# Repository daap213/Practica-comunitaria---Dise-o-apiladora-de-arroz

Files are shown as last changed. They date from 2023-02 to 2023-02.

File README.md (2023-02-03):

# Diseño y análisis de viabilidad de una apiladora de arroz usando energía renovable 

## Ilustració del diseño CAD-Solución:



## Ilustració del circuito:



## Autores ✒

* **Daniel Alvarado Pelaéz** 
* **Marcelo Mendoza Hidalgo**

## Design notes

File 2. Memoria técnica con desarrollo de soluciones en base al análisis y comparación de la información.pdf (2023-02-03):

## Aprovechamiento de recursos para un desarrollo sustentable en Paipayales

## Desarrollo de soluciones en base al análisis y comparación de la

información.

## Integrantes: Marcelo Mendoza Hidalgo, Daniel Alvarado Peláez

Comparación: Potencia, costo y capacidad de piladoras en diferentes mercados.

Se realizó la búsqueda pequeña de diferentes maquinas con la función de pilar arroz,

sea piladoras de múltiples granos, o maquinas moledora, trilladora, piladora de arroz,

## etc. Para así poder comparar principalmente su capacidad de productividad de arroz, el

## requerimiento de potencia del proceso y el costo de la máquina, claro que existen varios

## factores que influyen en el costo y en la potencia requerida, pero esta investigación nos

## dará una idea aproximada de que potencia sería necesaria para cierta capacidad

deseada y el costo que podría tener si se desea adquirir una en el mercado actual.

## Otros factores que se anotaron es la referencia de donde se encontraron las

## maquinarias, cuál era su fuente de energía, a base de combustible como gasolina o

## diésel, o energía eléctrica de 110V, 220V, 380V o 400V y por último el tamaño que cada

proveedor consideraba tenía la máquina.

## Cabe resaltar que la mayoría de estos datos se hallaron en sitios web de comercio

## electrónico como: mercadolibre y Alibaba. Y que no todos contaban todos los campos

## de información que requeríamos, por lo que los gráficos realizados posteriormente se

basan únicamente en aquellas referencias que si cumplen con lo que se desea estudiar.

## Base de datos realizada:

## Tabla 1 Maquinas piladoras: Costo en ($), Potencia en (HP) y capacidad en (Kg/h)

EMPRESA | Tipo | Precio ($) | Potencia (HP) Capacidad (kg/h) DESCRIPCION CODIGO/MODELO/DISTINTIVO TAMAÑO
Torotrac | DIESEL | | 12,00 | 300,00 | MULTIGRANO | PS0000535 | MEDIANA
Torotrac | ELECTRICA 220V | | 2,00 | 150,00 | MULTIGRANO | PS0000989 | PEQUEÑA
Torotrac | GASOLINA | | 5,50 | 150,00 | MULTIGRANO | PS0000983 | PEQUEÑA
Torotrac | DIESEL | | 20,00 | 800,00 | ARROZ GENERICA | PS0000144 | GRANDE
Torotrac | DIESEL | | 20,00 | 800,00 | ARROZ SATAKE | PS0000143 | GRANDE
Torotrac | ELECTRICA 220V | | 2,00 | 220,00 | ARROZ | PS0000145 | PEQUEÑA
Torotrac | GASOLINA | | 5,50 | 160,00 | ARROZ | PS0000991 | PEQUEÑA
Mercado libre | | 2.867,00 $ | 24,00 | 2.000,00 | | JING GU: SB-30GRANDE
Mercado libre | ELECTRICA 220V | 640,00 $ | | 150,00 | ARROZ | | PEQUEÑA
Mercado libre | ELECTRICA 220V | 1.800,00 $ | 15,00 | 1.000,00 | ARROZ | JING GU: SB-10GRANDE
Mercado libre | ELECTRICA 400V | 22.200,00 $ | 14,75 | 5.000,00 | ARROZ | MLGQ36 | GRANDE
Clasf | ELECTRICA 220V | 1.875,00 $ | 3,00 | 300,00 | PILADORA-TRILLADORA DE ARROZ SPHNM-300 | | PEQUEÑA
La Cobacha | ELECTRICA 110V | 650,00 $ | 2,68 | 120,00 | ARROS | POWER BULL: 6N40 PEQUEÑA
Mercado libre | ELECTRICA 220V | 1.195,00 $ | | 300,00 | Trilladora Descascaradora Piladora De Arroz PEQUEÑA
Mercado libre | ELECTRICA 220V | 1.760,00 $ | | 500,00 | ARROZ | | MEDIANA
CROPER | ELECTRICA 220V | | 7,50 | 120,00 | PILADORA-TRILLADORA DE ARROZ PEQUEÑA
Mercado libre | ELECTRICA 220V | 1.800,00 $ | 3,00 | 200,00 | ARROZ | 6N-J40 | MEDIANA
Mercado libre | ELECTRICA 220V | 1.463,00 $ | 3,00 | 150,00 | MULTIGRANO | YUNINLI: J 4 | PEQUEÑA
Mercado libre | ELECTRICA 220V | 1.514,00 $ | 3,00 | 200,00 | MULTIGRANO | YUNINLI: J 40 PEQUEÑA
Mercado libre | ELECTRICA 220V | 1.638,00 $ | 3,00 | 150,00 | MULTIGRANO | YUNINLI: J 220PEQUEÑA
Mercado libre | ELECTRICA 220V | 1.743,00 $ | 4,00 | 200,00 | PILADORA-TRILLADORA DE ARROZ YUNG: J 40 | | PEQUEÑA
Alibaba | ELECTRICA 380V | 2.500,00 $ | 7,40 | 3.000,00 | PILADORA-TRILLADORA DE ARROZ MLGT SERIES Rubber roll husker for rice milling plant GRANDE
Alibaba | ELECTRICA 220V | 2.000,00 $ | 7,40 | 2.000,00 | PILADORA-TRILLADORA DE ARROZ | ANON mini rice huller | GRANDE
Alibaba | ELECTRICA 380V | 4.572,00 $ | 14,75 | 5.600,00 | MULTIGRANO | MLGQ51-001 | GRANDE
Indiamart | | 243,00 $ | 20,00 | 1.000,00 | ARROZ | Dharti | PEQUEÑA
Indiamart | | 243,00 $ | 3,00 | 140,00 | ARROZ | Dharti | PEQUEÑA
Alibaba | ELECTRICA 220V | 120,00 $ | 3,00 | 180,00 | ARROZ | HELI 6N-40 | PEQUEÑA
Alibaba | ELECTRICA 380V | 1.800,00 $ | 30,00 | 2.000,00 | ARROZ | MG-N200 | PEQUEÑA
Alibaba | ELECTRICA 220V | 380,00 $ | 3,00 | 250,00 | ARROZ | HL-6N229 | PEQUEÑA
Alibaba | ELECTRICA 220V | 490,00 $ | 4,00 | 250,00 | ARROZ | KYM-RM6 3/4PEQUEÑA
Alibaba | ELECTRICA 380V | 600,00 $ | 7,40 | 1.500,00 | ARROZ | FORMEND LM24.2C PEQUEÑA
Alibaba | ELECTRICA 220V | 1.000,00 $ | 2,00 | 150,00 | PILADORA-TRILLADORA DE ARROZ DINGXIN 6HW47PEQUEÑA

## Gráficos comparativos:

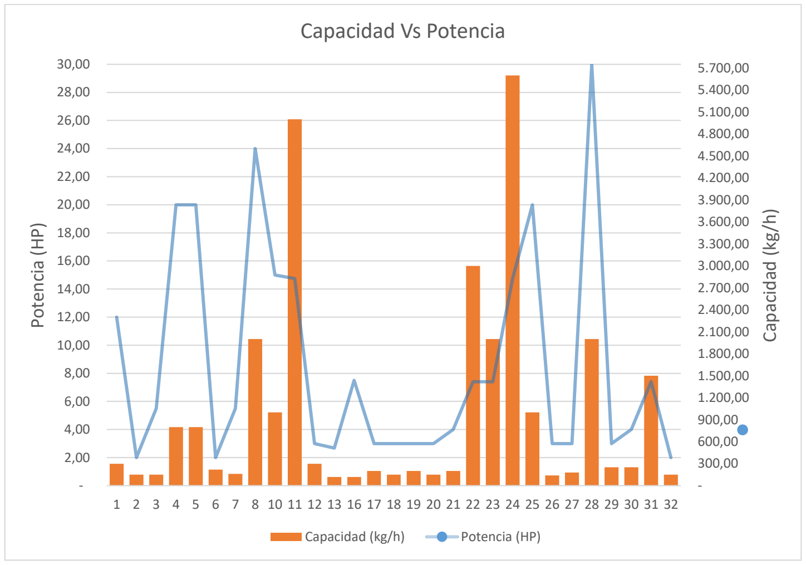
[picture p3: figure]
Capacidad (kg/h); Potencia (HP); Capacidad Vs Potencia

## Este grafico utiliza todos los datos que cuentan con potencia y compara la capacidad de

## la maquina piladora en Kg/h y la potencia que requiere en HP, siendo representados por

columnas y líneas respectivamente.

## La relación potenciada-capacidad es difícil de ver, dado que la potencia que se requiera

## puede aumentar si se realiza funciones además de pilar, como se realiza estos

## procedimientos, y el diseño mismo de la maquina influye en la eficiencia con la que se

## utiliza la potencia. Aun así en las algunas zonas donde las columnas seguidas de

capacidad tienden al mismo, la potencia también tiende a un mismo valor.

1 2 3 4 5 6 7 8 10 11 12 13 16 17 18 19 20 21 22 23 24 25 26 27 28 29 30 31 32

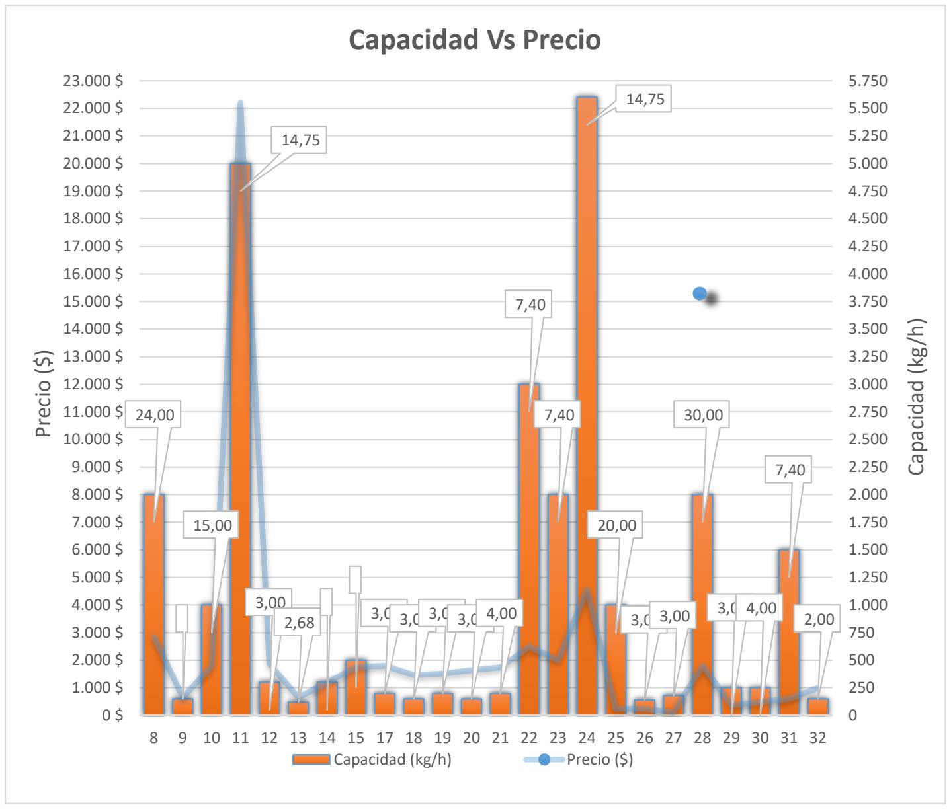
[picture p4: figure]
Capacidad (kg/h); Precio ($); Capacidad Vs Precio

## Este grafico utiliza todos los datos que cuentan con precio y compara la capacidad de la

## maquina piladora en Kg/h y el valor que tiene, siendo representados por columnas y

## líneas respectivamente, además en caso de que la maquina tenga registrada su

potencia, esta aparece como etiqueta.

## En general se aprecia que los puntos más altos de capacidad varían enormemente con

## el precio, debido a que han de contar con otras funciones o mejor calidad en cuanta

## maquinaria, pero con capacidades bajas como de 600 Kg/h se puede observar una

tendencia más estable.

2,68 3,00 3,00 3,00 3,00 4,00 | 3,00 3,00 | 3,00 4,00 | 2,00

8 9 10 11 12 13 14 15 17 18 19 20 21 22 23 24 25 26 27 28 29 30 31 32

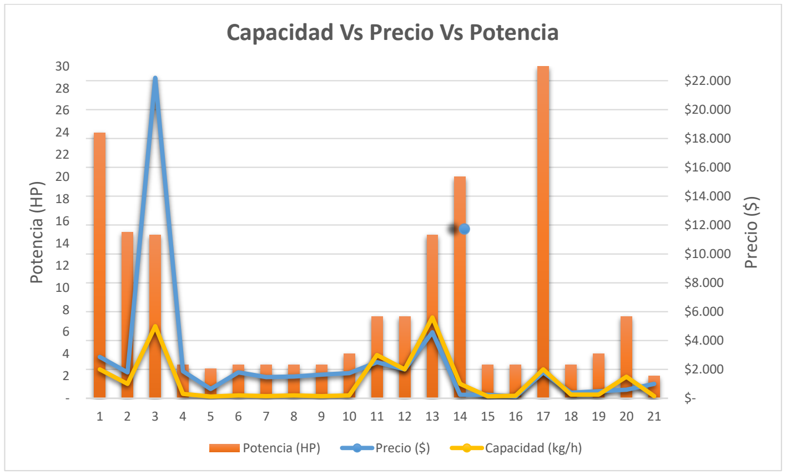
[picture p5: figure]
Potencia (HP); Precio ($); Capacidad Vs Precio Vs Potencia; Capacidad (kg/h)

## En este último grafico se utilizan todos los datos que cuentan con precio y potencia para

## comparar el costo de la maquina versus la potencia que requiere, siendo representados

## por líneas azules y columnas anaranjadas respectivamente, además la capacidad de la

## maquina piladora se ve representada con líneas amarillas, aunque no cuenta con una

## representación numérica, sirve para dar una idea de la relación potencia-costo-

capacidad.

## Se puede observar que para potencias menores a 8 HP, los precios tienen cierta

## tendencia estable, Lo que nos una idea de que valor podría tener una pilladora que

requiera 3HP, además en conjunto la capacidad de 100 kg/hora requerida.

1 | 2 | 3 | 4 | 5 | 6 | 7 | 8 | 9 10 11 12 13 14 15 16 17 18 19 20 21

Referencias:

### https://es.scribd.com/document/380323860/Modelos-de-Maquinas-Piladoras-Arroz

### https://www.sangatiberga.com.br/es/produtos/arrozeras/descascaradora-de-arroz-sbr-sd

### https://www.torotrac.com/product/OE-Piladora%20de%20Maiz-%20Piladora%20de%20Cafe%20-%20Piladora%20de%20Arroz

### https://www.torotrac.com/product/OE-Piladora-2

### https://www.torotrac.com/product/OE-Moledora-PS0000981

### https://www.torotrac.com/product/OE-Piladora-1

### https://www.torotrac.com/product/OE-Piladora-PS0000980

### https://www.torotrac.com/product/OE-Piladora-PS0000989

### https://es.made-in-china.com/co_ueindus/product_Mini-Small-Rice-Mill-for-Home-Use_rgieeurng.html

### https://www.suriaenergy.com/de-motores-electricos-y-energia-solar

### https://www.muyinteresante.es/innovacion/articulo/motores-stirling-para-obtener-energias-renovables

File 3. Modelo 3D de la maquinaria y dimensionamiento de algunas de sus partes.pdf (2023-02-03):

Aprovechamiento de recursos para un desarrollo sustentable en Paipayales

Dimensionamiento y diseño de prototipo de bajo costo.

Integrantes: Marcelo Mendoza Hidalgo, Daniel Alvarado Peláez

Diseño Inicial de Piladora de Arroz

Se realizó el dibujo inicial de la piladora de arroz la cual debe producir 1 quintal de arroz

por hora. En base a los datos presentados previamente y a investigaciones anteriores,

se hizo la comparación de producción de arroz y de motores en base a su potencia,

estableciendo que el motor que se usará para nuestra aplicación será un motor de 3HP

que en próximos avances se revisará su implementación con energías renovables.

Con este dato se investigó diseños de piladoras que posean esa potencia, con ello se

tuvo una idea de la forma y tamaño adecuado aproximado que tendrá nuestro diseño el

cual se presenta a continuación (dimensión del motor sujeta a cambios):

Mesa de trabajo:

En esta pieza se asienta la máquina piladora se realizará del material adecuado para

absorber vibraciones

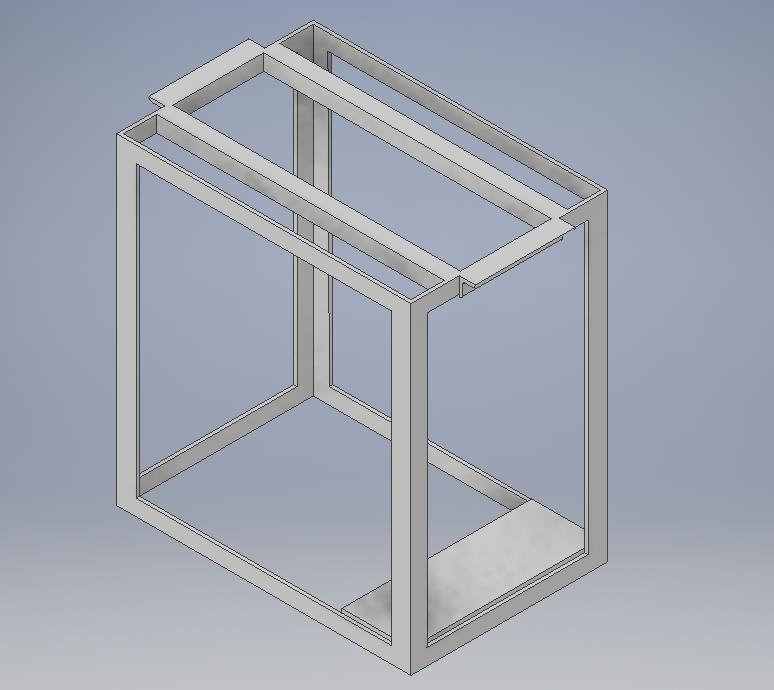
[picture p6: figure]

Parte exterior de la máquina:

Se puede observar en la parte superior el “embudo” en donde se colocará los granos de

arroz a descascarar, esta pieza sirve de carcasa para la parte interna de la máquina en

donde se separa el arroz de su cáscara.

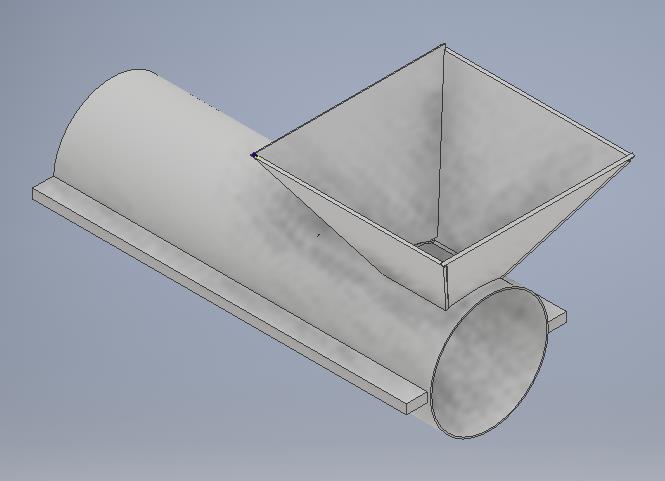
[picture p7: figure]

Eje de moler:

Esta parte de la máquina en su parte giratoria en forma de espiral se encarga de empujar

el arroz que ingresa y a continuación molerlo o desprenderlo de su cáscara mediante las

partes más salidas del eje que tienen contacto con la carcasa mientras sigue con el

recorrido

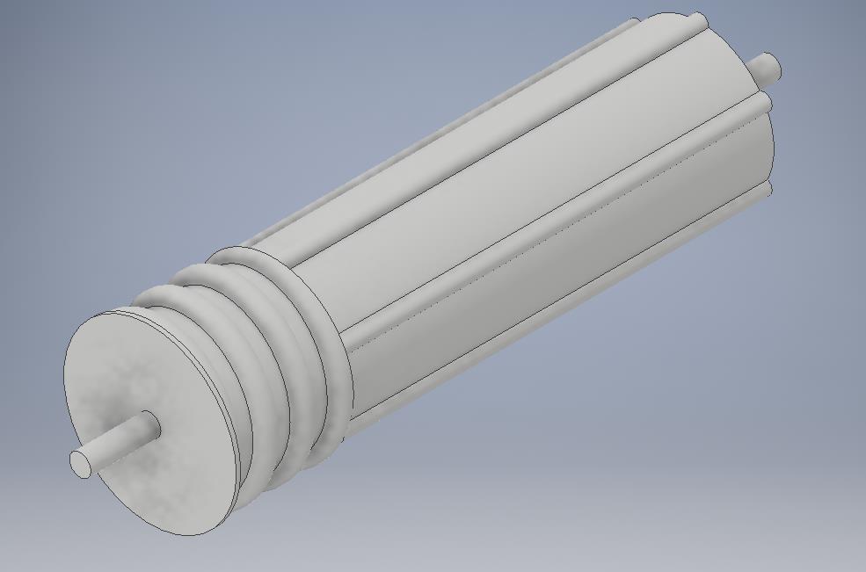
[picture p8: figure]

Pieza Cernidera:

Esta pieza se encuentra alrededor del eje de moler, la cual permitirá el paso de la

cáscara del arroz y no del arroz descascarado (como una cernidera). Con ello se puede

expulsar la cáscara del arroz por la parte de abajo de la máquina y permitiendo el paso

del arroz hacia el final del avance del eje en donde se encuentra una salida para el

arroz sin cáscara.

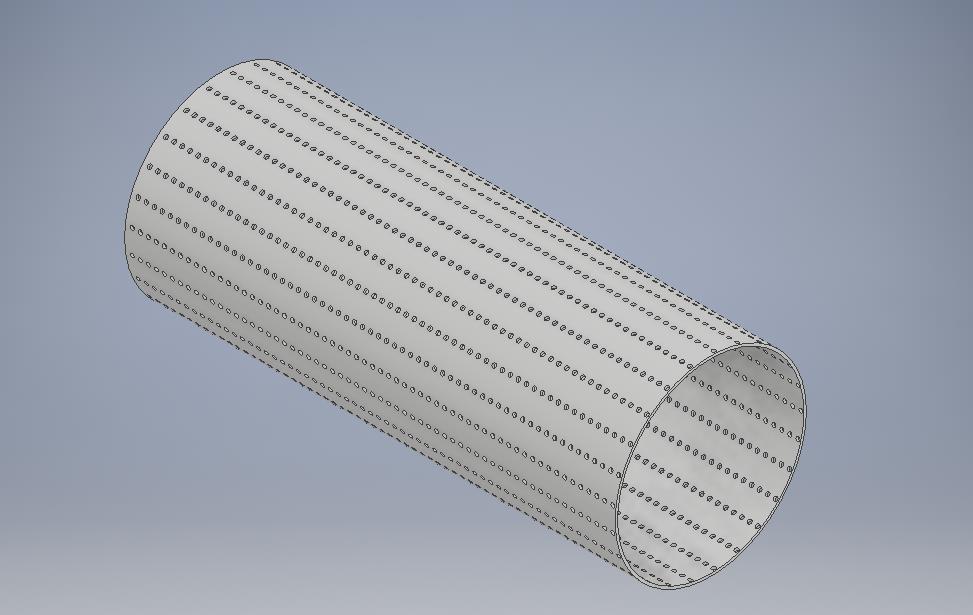
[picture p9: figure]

Ensamblaje:

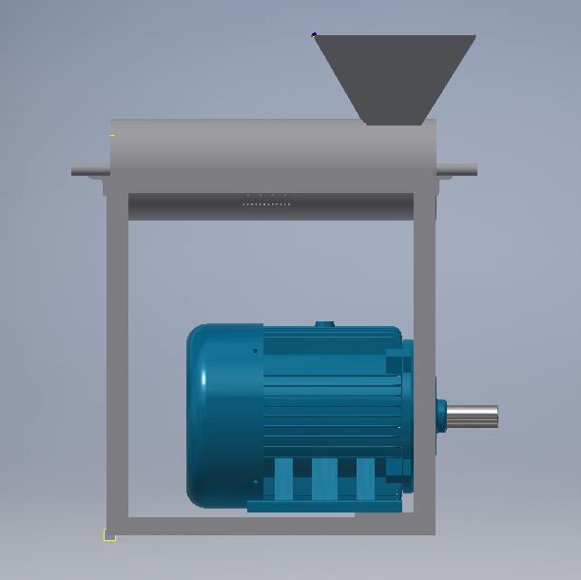
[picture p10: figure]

Aplicándole transparencia a la carcasa:

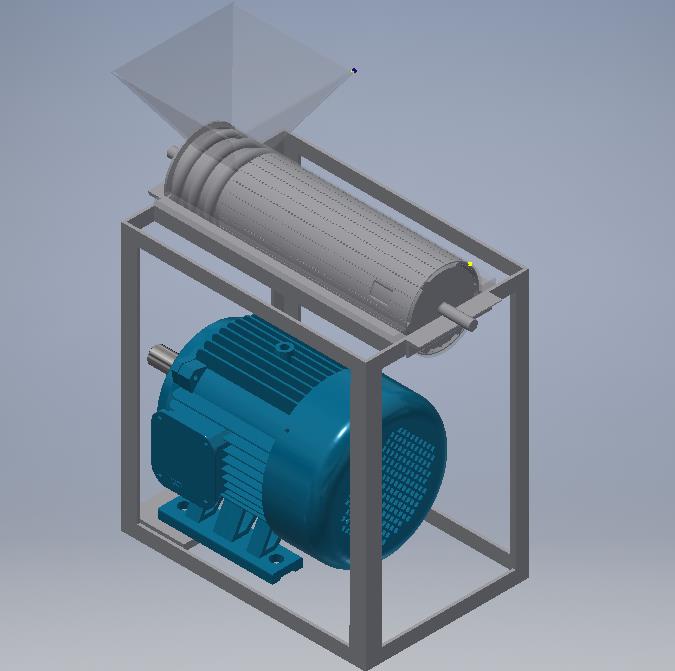
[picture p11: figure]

Aplicándole transparencia a la carcasa y cernidera:

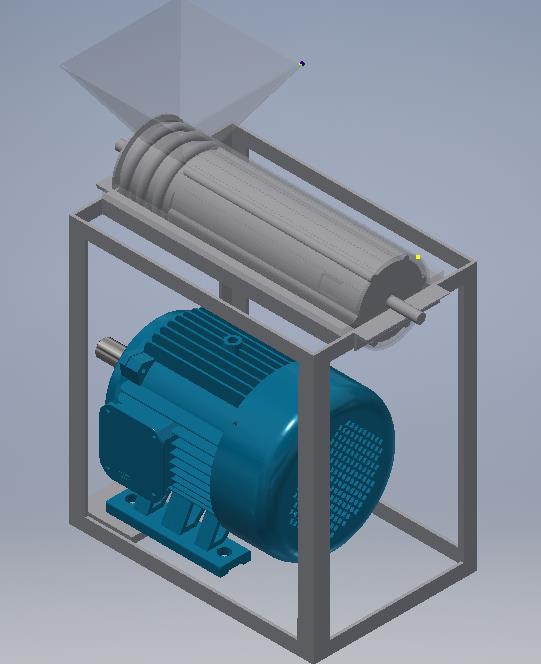
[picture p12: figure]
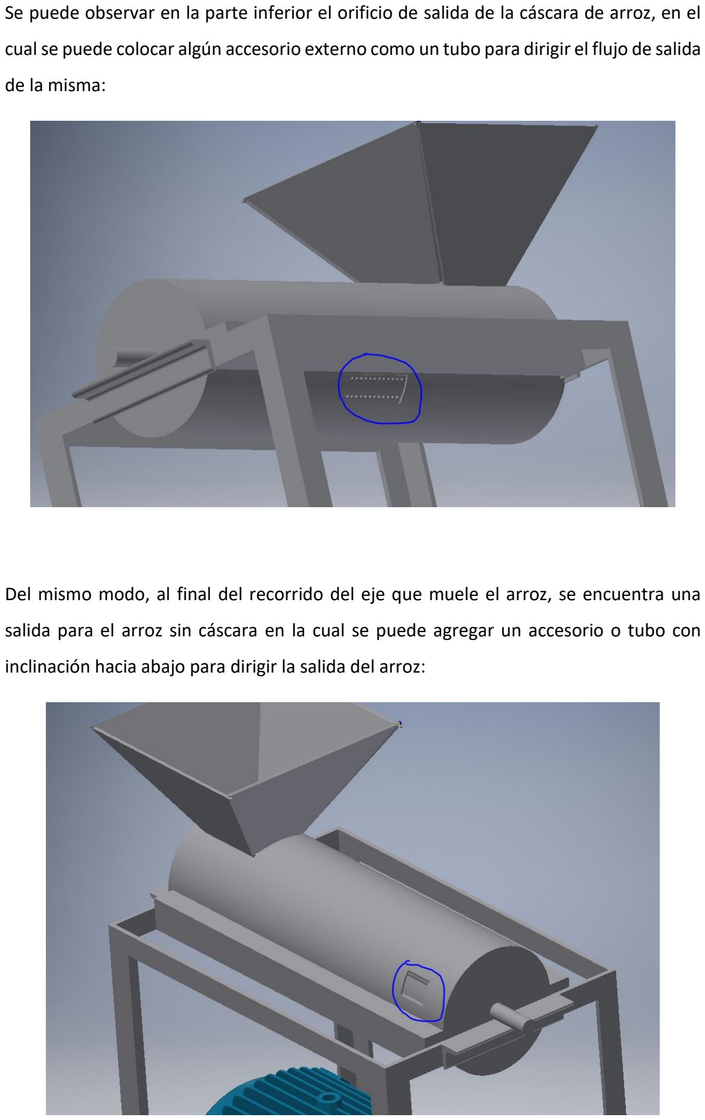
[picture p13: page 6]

Se puede observar en la parte inferior el orificio de salida de la cáscara de arroz, en el

cual se puede colocar algún accesorio externo como un tubo para dirigir el flujo de salida

de la misma:

Del mismo modo, al final del recorrido del eje que muele el arroz, se encuentra una

salida para el arroz sin cáscara en la cual se puede agregar un accesorio o tubo con

inclinación hacia abajo para dirigir la salida del arroz:

Diseño de un sistema de transmisión de potencia con una banda en V (Según el manual de SKF) entre el motor y el eje de trabajo de la piladora de arroz.

### 1. Planteamiento

El eje de trabajo de una piladora, según basándonos en máquinas similares, tiene una velocidad entre 750 y 1000 rpm para pilar hasta un 90% el arroz, para el diseño se usará una velocidad de 850 y un uso diario de hasta 8 horas.

El motor se encontrará debajo de este eje con una distancia menor o igual a medio metro y se asume que se usará en arranque directo un Motor Cerrado Eléctrico monofásico 3hp 1750 Rpm.

### 2. Corrección en la potencia

- Categorización del motor

Al ser un arranque directo se categoriza como un arranque fuerte.

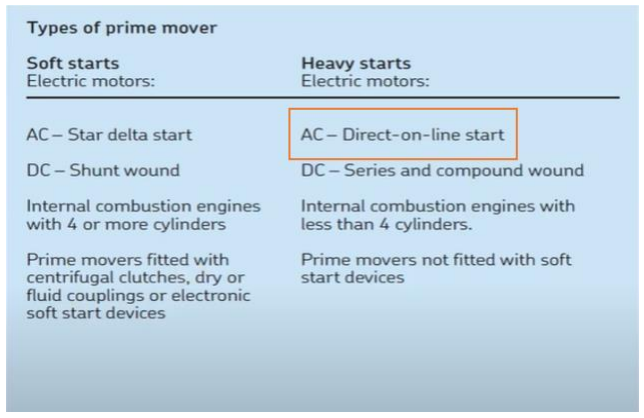
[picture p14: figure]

Ilustración 1 Categoría del motor

- Categorización de la carga

Se asume que la piladora podría trabajar un máximo de 8 horas al día, realizando la acción de pilar el arroz, que la consideramos como una carga pesada.

Por lo que el coeficiente de corrección es de 1,4.

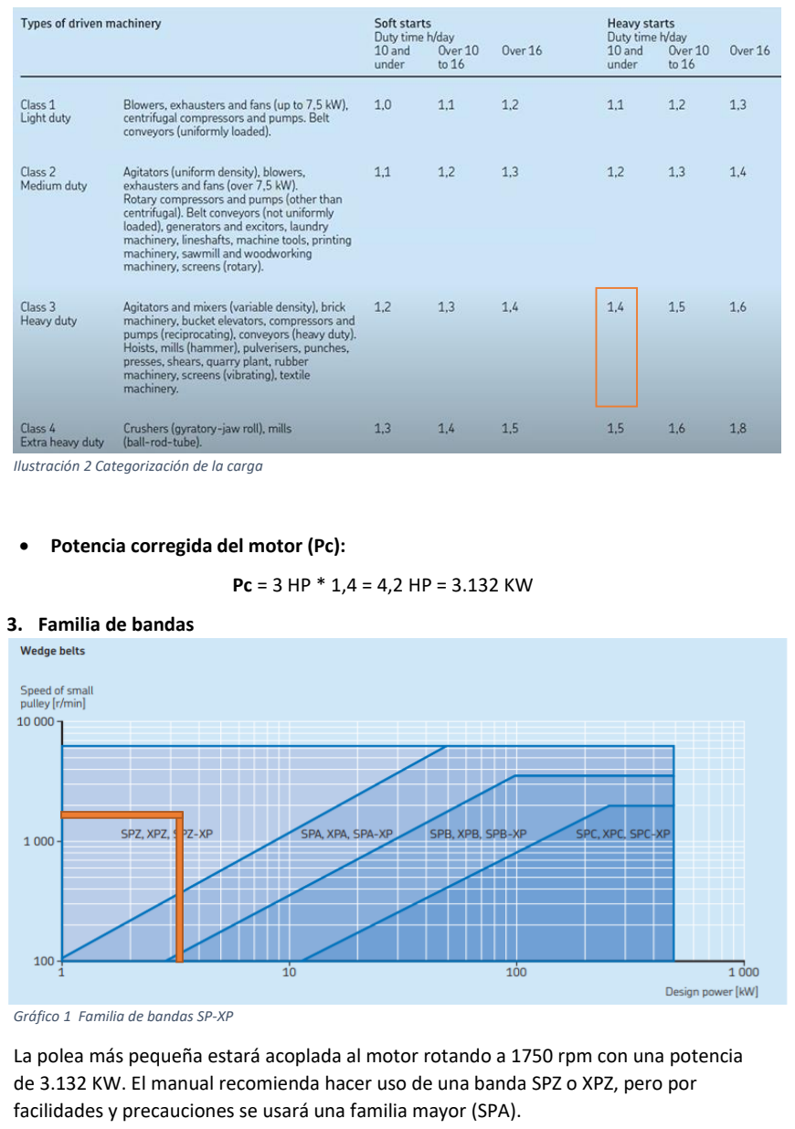
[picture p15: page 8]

Ilustración 2 Categorización de la carga

- Potencia corregida del motor (Pc):

Pc = 3 HP * 1,4 = 4,2 HP = 3.132 KW

### 3. Familia de bandas

Gráfico 1 Familia de bandas SP-XP

La polea más pequeña estará acoplada al motor rotando a 1750 rpm con una potencia de 3.132 KW. El manual recomienda hacer uso de una banda SPZ o XPZ, pero por facilidades y precauciones se usará una familia mayor (SPA).

### 4. Relación de velocidades

Se mencionó que el juego de poleas con banda en V reducirá la velocidad del motor 1750 rpm a 850 rpm para el eje.

Ir =

1750
850 = 2.06

### 5. Longitud de banda, diámetro de poleas

Se desea que la distancia entre centros sea máxima medio metro, con una relación de velocidad de 2.06, pero en la tabla no hay una relación igual, así que se escoge el máximo superior 2.10, después esta se puede ajustar con una polea tensora de ser necesario.

Así la distancia entre centros es de 324mm, la longitud de banda a usar es de 1400mm, el diámetro de la polea impulsadora (d) es de 150mm y de la polea impulsada (D) es de 315mm.

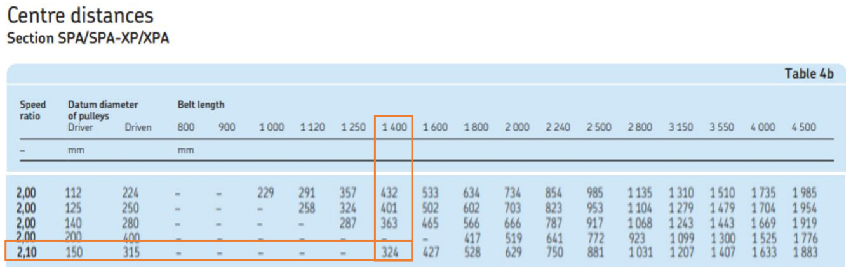
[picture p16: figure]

Tabla 1Distancia entre centros

### 6. Potencia nominal de una banda (Pb)

La potencia nominal más una potencia adicional en función de la relación de velocidad, que puede aguantar una banda SPA con una polea pequeña de 150mm a 1750rpm no se encuentra en la tabla, pero si en medio de 2 valores existentes, por lo que se asumirá como el valor intermedio:

Superior: 1800rpm –> (6.26 + 0.54) KW

Potencia nominal: 1350rpm -> (6.12 + 0.525) KW = 6.645 KW

Inferior: 1700rpm -> (5.98 + 0.51) KW

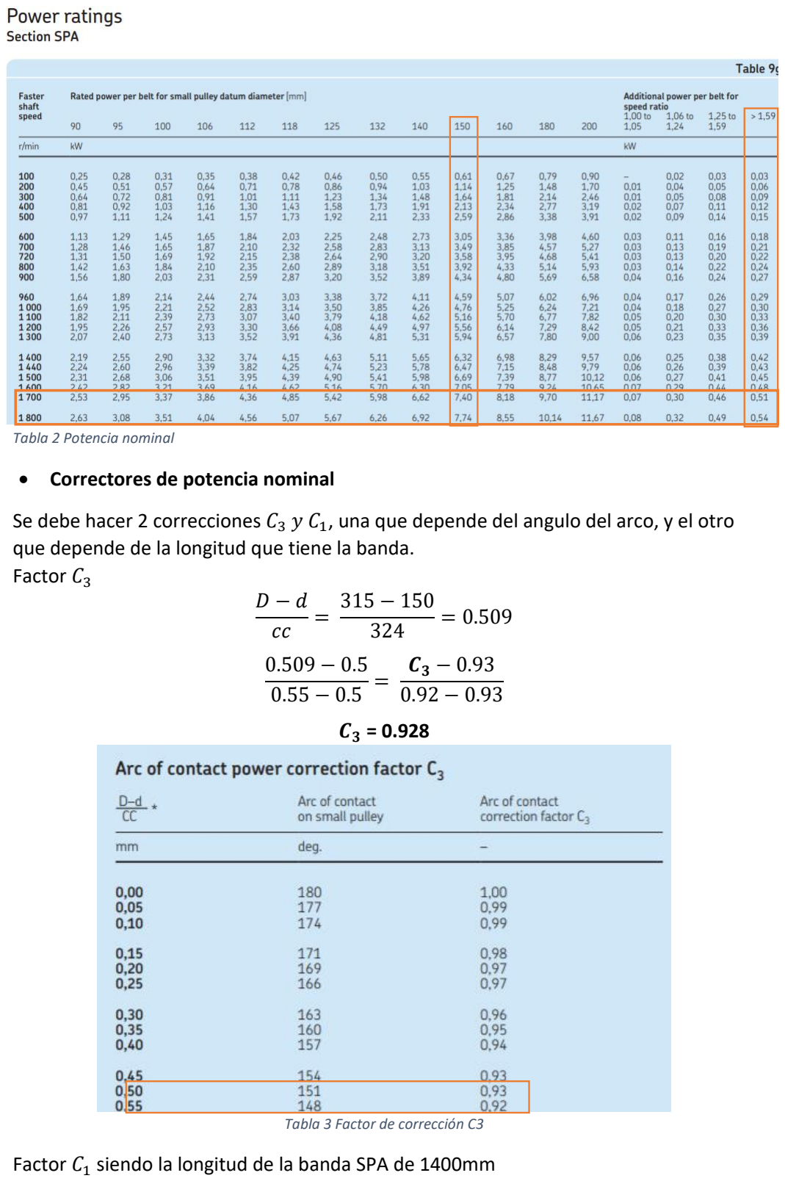
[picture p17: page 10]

Tabla 2 Potencia nominal

- Correctores de potencia nominal

Se debe hacer 2 correcciones C3 y C1, una que depende del angulo del arco, y el otro que depende de la longitud que tiene la banda.
Factor C3
D − d
cc

=

315 − 150
324 = 0.509

0.509 − 0.5
0.55 − 0.5
= | C3 − 0.93
0.92 − 0.93
C3 = 0.928

Tabla 3 Factor de corrección C3

Factor C1 siendo la longitud de la banda SPA de 1400mm

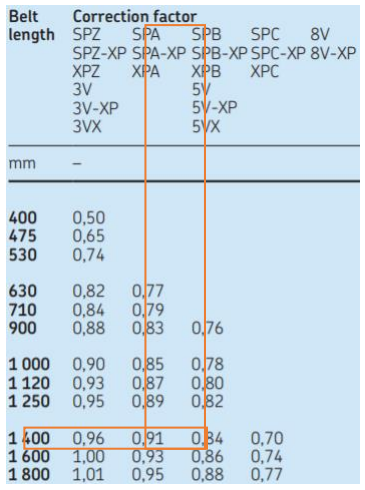
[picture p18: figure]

C1 = 0. 91
Tabla 4 Factor C1
- Potencia nominal corregida:

Pbc = Pb ∗ C1 ∗ C3 = 5. 612 KW

Una sola banda de SPA puede transmitir 6.07 KW, como la potencia de diseño 2,685KW es menor, entonces basta con una sola banda SPA para transmitir toda la potencia deseada.

### 7. Instalación

Para poder instalar, cambiar y tensar la banda se requieren de distancias mínimas y máximas entre los centros de las poleas en función de la longitud de la banda que es 1400mm.

MIA = 25mm; MTA = 35mm
Cmin = 324 - MIA = 299mm
Cmax = 324 + MTA = 259mm

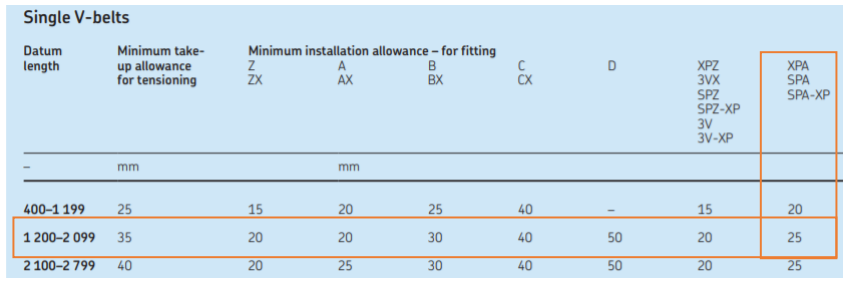
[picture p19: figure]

Tabla 5 MIA y MTA

### 8. Tensión recomendada

La marca recomienda una tensión de 5,7 Kgf cuando la banda es nueva, y 3,8 Kgf cuando ya se ha usado un poco.

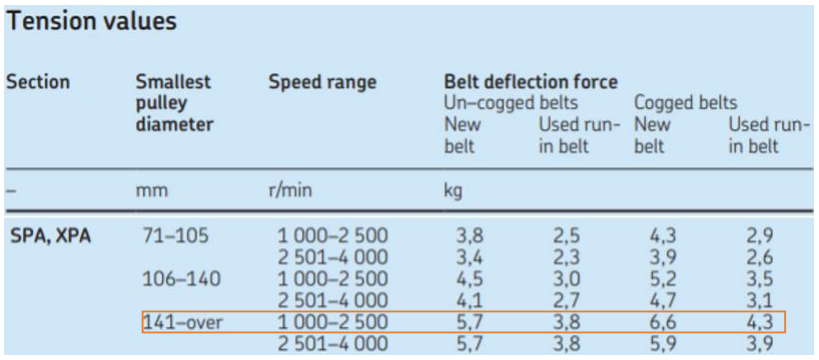
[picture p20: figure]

Tabla 6 Tensión recomendada

### 9. Tabla de datos de diseño

Potencia corregida | 3.132 KW
Relación de velocidad | 2.1
Diámetro polea impulsadora | 150 mm
Diámetro polea impulsada | 315 mm
Distancia entre poleas | 324 mm
Familia de banda | SPA
Longitud de la banda | 1400 mm
Potencia nominal de la banda | 5.612 KW
MIA | 25 mm
MTA | 35 mm
Tensión mínima | 3,8 Kgf

### 10. Detalles de la banda SPA según SKF

Ilustración 3 Detalles de la banda SPA

### 11. Diseño en inventor 2019

Se modela los datos requeridos y supuestos en inventor dando como resultado una simulación aproximada de las tensiones de la banda en V (F1, F2) y la fuerza que siente el eje de trabajo (Rx).

F1 = 79,464 N; F2 = 242,220 N Fuerza axial en el eje (Rx) = 313,841 N

Ilustración 4 Medidas de diseño en Inventor 2019

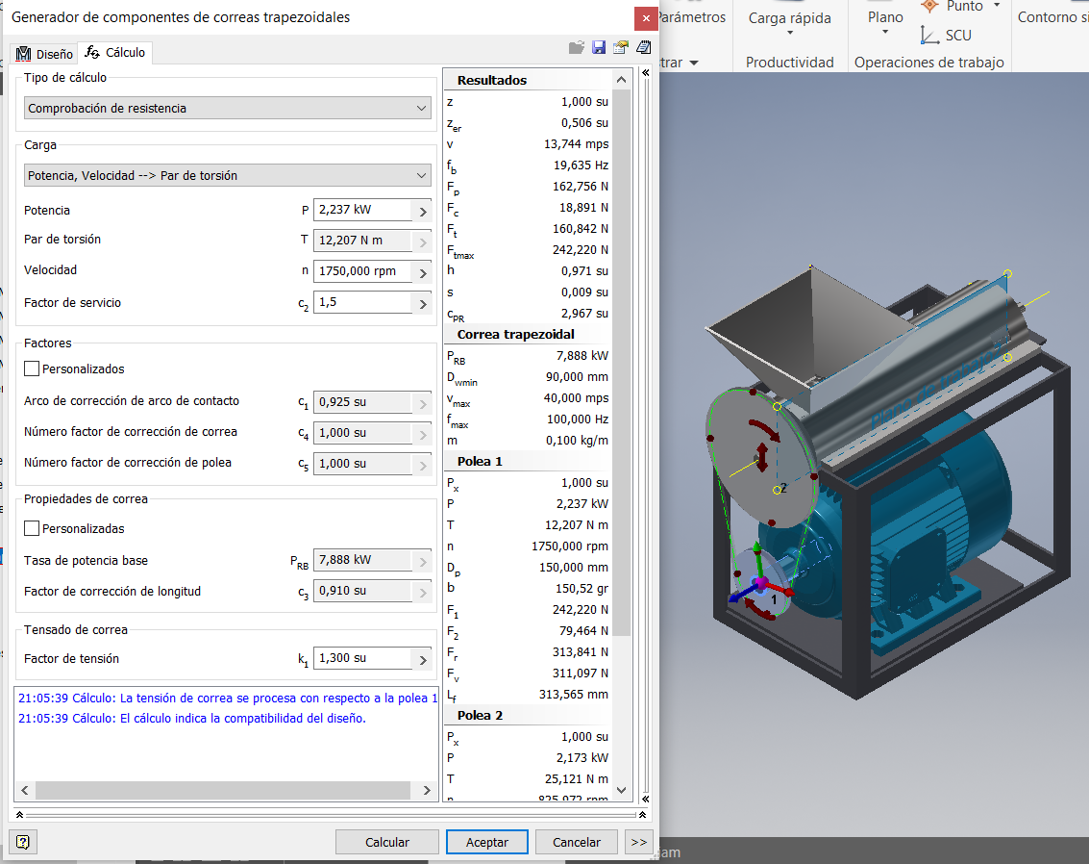
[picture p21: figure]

Ilustración 5 Cálculos de diseño de la banda en V

Selección de rodamientos:

Es importante tomar en cuenta ciertas características conocidas previamente para la selección de los rodamientos:

- Diámetro interior: El eje cuenta con un diámetro de 25 mm en donde estarán ubicados los rodamientos.
- Velocidad de rotación: El eje contará con una velocidad de rotación de 850 rpm
- Cargas radiales: Las cargas a tomar en cuenta son de 242.2 N y 313,8 N

Del mismo modo es importante estimar ciertos datos para el análisis de la selección:

- Espacio del alojamiento: El espacio de alojamiento máximo para los rodamientos será de 55mm
- Vida máxima del rodamiento: La vida útil mínima que tendrá el rodamiento será de mínimo unas 4400 horas (Aproximadamente 1 año y medio trabajando 8 horas diarias)
- Carga axial: Se debe escoger una carga axial para el rodamiento, en este caso se estimará que este es del 1%.
- Temperatura: Se estima que la temperatura no pasará de los 80°C

- Tipo de lubricación: Dado que la velocidad de rotación y la temperatura no son valores sumamente altos, se recomienda usar una lubricación por grasa.
- Tipo de rodamiento: Se utilizará rodamiento rígido de bolas.

Una vez mencionado los parámetros previos, se utilizará la calculadora de rodamientos perteneciente a SKF en donde se obtendrán los siguientes resultados propuestos:

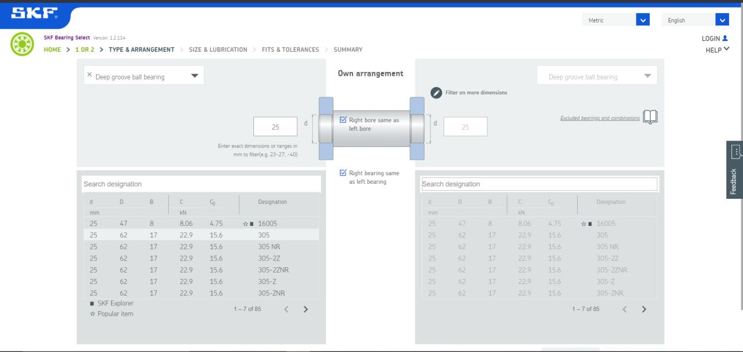
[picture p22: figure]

se puede apreciar como los datos y parámetros de diámetro interior y tipo de rodamiento ya han sido seleccionados, y a continuación se hará uso de los rodamientos marcados con la designación de 305 para ambos rodamientos.

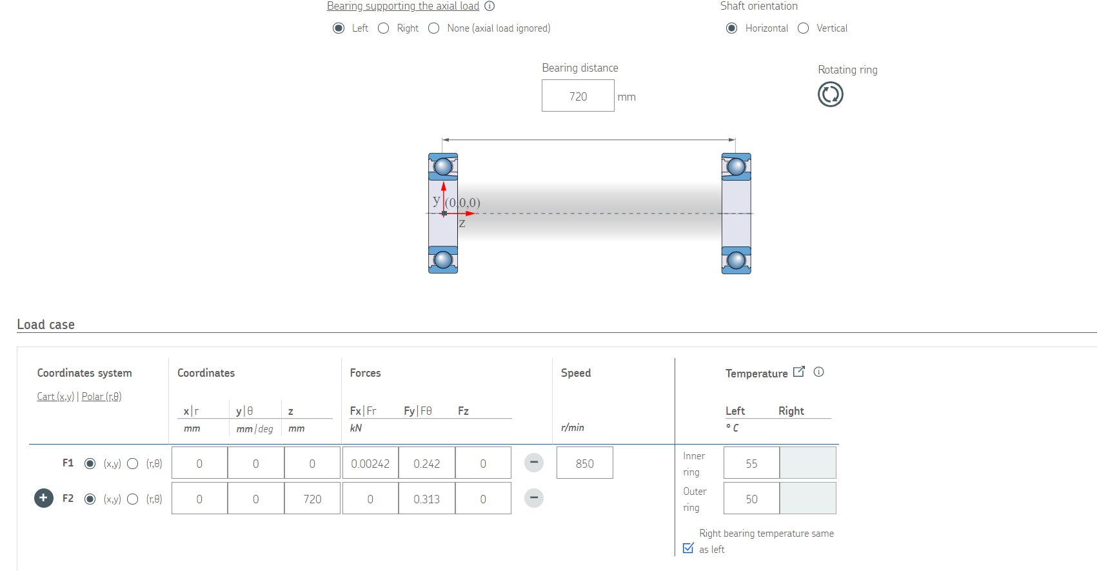
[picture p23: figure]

Se muestran las distancias en las cuales están ubicados los rodamientos, las cargas aplicadas, la velocidad en rpm, la temperatura a la cual estos trabajar siendo esta una temperatura de 55°C por dentro del anillo y 50°C por fuera, además de haber seleccionado al rodamiento izquierdo como aquel que se mantendrá fijo.

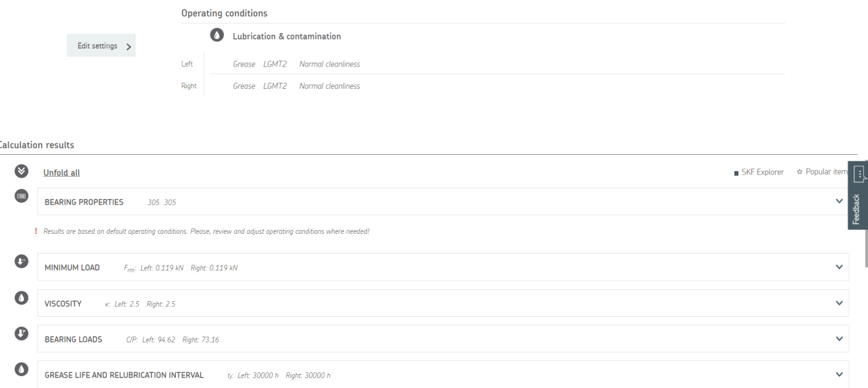
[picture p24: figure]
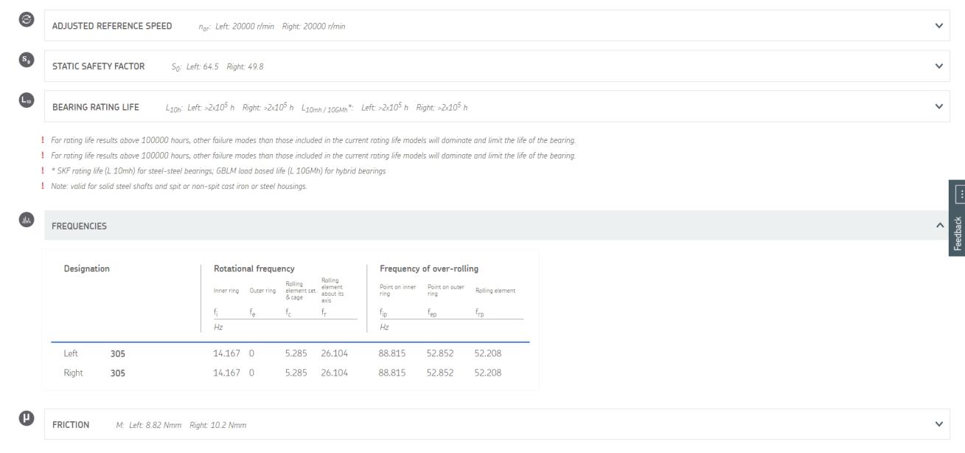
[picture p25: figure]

En base a los parámetros escogidos previamente, se obtuvieron los siguientes resultados siendo algunos de estos la carga mínima de 0.119 KN además del tiempo para una nueva lubricación de 30000 horas, por lo que cumple sobresalientemente el tiempo mínimo requerido. Se muestra también la velocidad de referencia siendo de 20000 rpm, la vida estándar del rodamiento de 200000 horas cumpliendo de igual forma el mínimo tiempo de vida requerido Estos y entre otros datos obtenidos se encuentran en las imágenes anteriores como resultados de la calculadora de SKF.

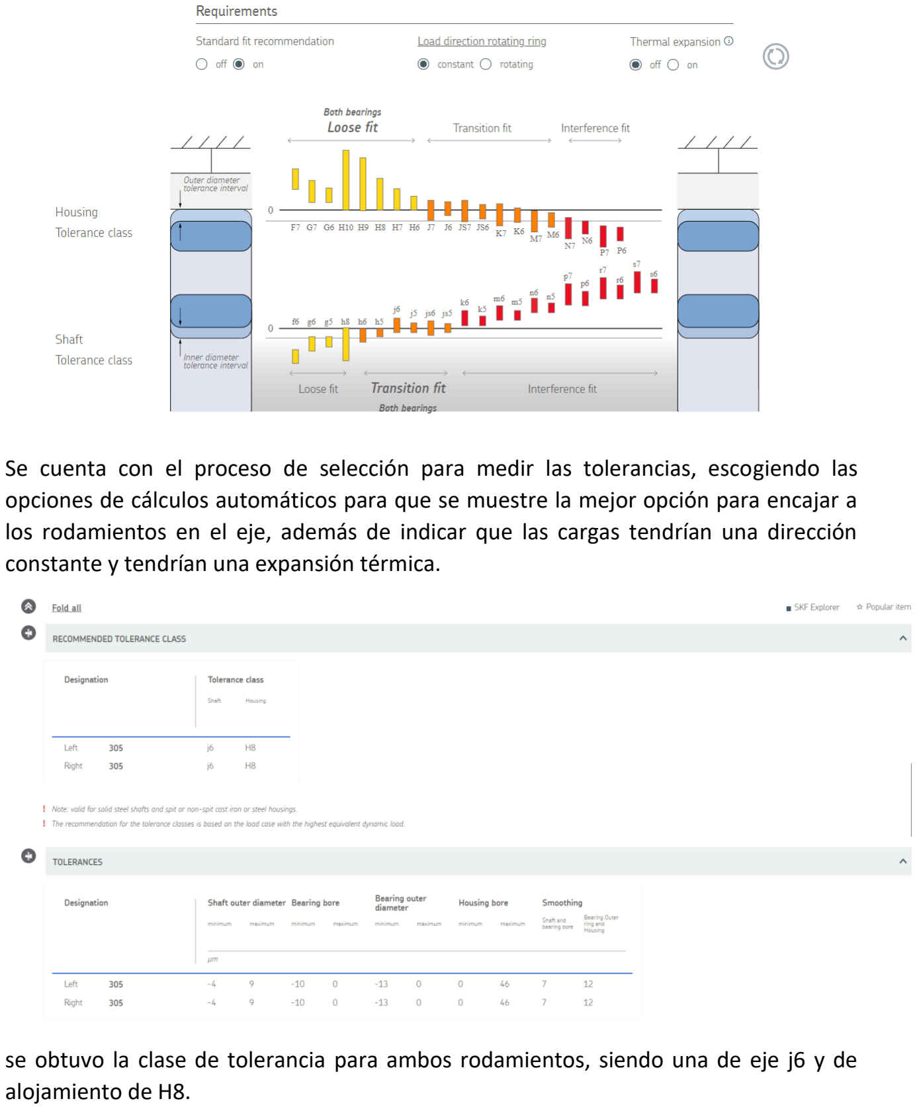
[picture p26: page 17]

Se cuenta con el proceso de selección para medir las tolerancias, escogiendo las opciones de cálculos automáticos para que se muestre la mejor opción para encajar a los rodamientos en el eje, además de indicar que las cargas tendrían una dirección constante y tendrían una expansión térmica.

se obtuvo la clase de tolerancia para ambos rodamientos, siendo una de eje j6 y de alojamiento de H8.


En las imágenes anteriores se muestran demás datos calculados mediante SKF entre los cuales se encuentra la condición de lubricación (k) de 2.5 y la carga de radio (C/P) de 94.62 y 73.16, factores de seguridad y pérdidas de potencia.

Se procede a realizar los rodamientos en el diseño de Inventor:


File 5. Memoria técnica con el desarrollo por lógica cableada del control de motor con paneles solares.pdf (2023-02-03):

Aprovechamiento de recursos para un desarrollo sustentable en Paipayales

Desarrollo del control del motor con paneles solares.

Integrantes: Marcelo Mendoza Hidalgo, Daniel Alvarado Peláez

Kit para obtención de energía solar 3hp:

El kit escogido para la obtención de la potencia necesaria a partir de energía solar para la máquina piladora de arroz cuenta con las siguientes partes además de los cables para las conexiones:

Inversor solar: Está integrado con un cargador solar para maximizar la energía obtenida. Además, es fácil de instalar con un bajo costo de mantenimiento. Se convierte en una solución ecológica para las zonas rurales, donde la red eléctrica es cara y poco confiable. La potencia de salida es de 3hp


Paneles solares: Se cuenta con 14 paneles solares de 144 celdas cada uno. Captan la energía del sol para ser posteriormente convertida a energía eléctrica. Alta eficiencia de conversión de módulo de hasta 20,58%


Fusibles fotovoltaicos: Los fusibles fotovoltaicos se utilizan en la caja auxiliar del arreglo fotovoltaico, para protección contra sobrecargas y cortocircuitos entre los módulos fotovoltaicos y el inversor.


Protector contra descargas atmosféricas: Protege los aparatos eléctricos de los rayos y sobretensiones instantáneas


Desarrollo del control del motor con paneles solares.

3ℎp = 2.2 KW

Consumo aproximado de la piladora de 8 horas diarias.

2.2 KW ∗ 8ℎoras = 17.6 KWℎ/día

Se plantearía el uso del kit con una Batería Ritar 12V 100A*h RA AGM Libre Mantenimiento


Con una de estas baterías se tiene:

12V =

100A ∗ ℎ
1000 = 1.2 KWℎ/día

17.6
1.2

= 14.66 ≈ 15

Por lo tanto, se necesitan de 15 baterías para lograr los 17.6 kwH/día que se usara en el uso de la piladora.

En base a estos datos se desarrolló la simulación del circuito y su control en el programa Cade_Simu como se muestra a continuación:

Conexión de paneles solares:


Protección del inversor de la energía proveniente de los paneles:


Esquemático para el control del motor:


Esquemático para el motor:


Circuito final:


Para el circuito se realizó la conexión en serie de los 14 paneles que se cuentan en el kit para la obtención de la potencia de 3hp. Estos paneles almacenan su energía en las baterías ya mencionadas anteriormente. Se contará con 15 baterías para poder obtener la potencia requerida en el sistema.

Se cuenta con un circuito para la protección del inversor el cual se usa para convertir correctamente la energía solar a energía eléctrica y maximizar su uso. El circuito de protección cuenta con fusibles fotovoltaicos y disyuntores, a su vez con protector contra descargas atmosféricas.

Este voltaje es otorgado al circuito de fuerza que es donde se encuentra el motor, el cual cuenta también con un disyuntor para protección y un relé térmico que avisará en caso de sobre temperatura.

El circuito de control cuenta con un disyuntor de protección, interruptor normalmente abierto para el encendido del sistema y uno normalmente cerrado para el apagado. A su vez cuenta con una bobina y un contactor para poder realizar el enclavamiento una vez se accione el interruptor de encendido. Se cuenta con un led indicador de encendido y otro que indica si el relé térmico se ha activado.


Simulación del control del motor:

Estado inicial:

Se activan los disyuntores de ambos circuitos:

Se activa el switch para el encendido del motor, el motor permanece encendido debido al enclavamiento causado gracias al contactor KM y su respectiva bobina.

Se cuenta con un led verde que indica que el motor se encuentra encendido.


Se cuenta con un relé térmico que se activa en caso de sobrecalentamiento en el motor, el cual encenderá un led rojo que da un aviso al usuario.

Referencias:

https://solar-energia.net/energia-solar-fotovoltaica/elementos/baterias-solares

https://www.panelsolarperu.com/productos/21-bateria-ritar-12v-100ah-ra-agm-libre-mantenimiento.html (https://www.panelsolarperu.com/productos/21-bateria-ritar-12v-100ah-ra-agm-libre-mantenimiento.html)

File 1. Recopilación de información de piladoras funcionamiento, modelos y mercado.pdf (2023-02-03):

Aprovechamiento de recursos para un desarrollo sustentable en Paipayales

Investigación de información acerca de piladoras de arroz y de energía renovable en base a ejemplos reales

Integrantes: Marcelo Mendoza Hidalgo, Daniel Alvarado Peláez

Piladoras de arroz:

Las piladoras de arroz son máquinas destinadas a descascarar y limpiar el arroz, dejándolo listo para el consume. Se las conoce también como molinos de arroz o máquinas de descascarado de arroz.

Proceso:

El arroz, después de secado en los secaderos, pasa por los siguientes procesos:

1. Descascarado. Proceso en el cual a los granos se les separa la cáscara (envoltura exterior). Es obtenido a través de la acción de la fricción realizada por una pareja de rollos en rotación con velocidades diferentes

2.Pulido. Consiste en eliminar la membrana de salvado, dejando el gano (endospermo) completamente pulido.

La máquina consta de 5 partes: la tolva de carga, caja de descascarado, dispositivo de transmisión, dispositivo de separación y la base para la máquina.

El grano llega a la máquina a través de la tolva de carga y luego pasa a la cámara de pilado mediante el tornillo de alimentación. La sección de descascarado puede producir una gran presión, el germen y el salvado del grano se pelan gracias a la fricción entre el rodillo y el tamiz.

Equipamiento de las pilladoras

1.Descascaradora. Máquina que realiza el descascarado de forma automática, por lo regular combinándolo con un proceso de aventado. Por lo regular está formada por cilindros o discos que giran en sentido inverso entre sí, y rompen la cubierta exterior del grano (cáscara).

2.Brilladora. Máquina que separa la membrana de salvado y otras partículas, quedando el grano listo para el consumo.

Capacidad de las piladoras de arroz:

Las máquinas piladoras de arroz tienen ciertas características que cumplen según la calidad de la máquina:

Pre Limpieza: Eliminación de todas las impurezas y granos sin relleno del arroz crudo

De-lapidación: Separación de piedras pequeñas de arroz

Descascarillado: Quitar la cáscara del arroz

Aspiración de la cascara: Separación de la cáscara del arroz integral / arroz sin cascara

Separación de arroz: Se separa el arroz

Blanqueo: Eliminar toda o parte de la capa de salvado y el germen del arroz integral

Pulido: Mejorando la apariencia del arroz molido al eliminar las partículas restantes de salvado y puliendo el exterior del grano molido

Clasificación de longitudes: Separación de tamaños pequeños y grandes del arroz de cabeza

Mezcla: Mezcla del arroz con otros componentes según lo requiera el cliente.

Pesaje y embolsado: Preparación del arroz molido para el transporte al cliente.

Características de los granos de arroz

Los granos de arroz tienen tres partes componentes fundamentales:

* Endospermo. Es el interior del grano, de color blanco, que es la parte comestible fundamental.

* Membrana. Separa al grano de la cáscara y constituye lo que comúnmente se denomina salvado, y que se elimina en el proceso de brillado. El salvado del grano tiene proteínas y vitaminas E, K y del complejo B. El arroz blanco, que es el grano privado del salvado nutritivo, es un alimento de menor calidad, por lo cual los dietistas recomiendan consumir el llamado arroz integral, que es el grano que no se somete al brillado.

* Cáscara. Es la cubierta exterior de consistencia dura y color castaño, que protege al grano. Se emplea como combustible en los secaderos o como aditivo de los piensos.


Figura1. Ejemplo de máquina piladora de arroz

Energía renovable:

Son aquellas fuentes de energía basadas en la utilización de recursos naturales: el sol, el viento, el agua o la biomasa vegetal o animal. Se caracterizan por no utilizar combustibles fósiles, sino recursos naturales capaces de renovarse ilimitadamente.

Uno de sus puntos fuertes es que tienen un impacto ambiental muy escaso, pues además de no emplear recursos finitos, no generan contaminantes.

A las energías renovables se les conoce también como energías alternativas o energías verdes. (https://www.factorenergia.com/es/blog/autoconsumo/aumento-del-consumo-energia-verde/) Las energías renovables proceden de recursos naturales de acceso gratuito e inagotables

Las energías renovables, al generar la energía a través de fuentes naturales, se pueden encontrar en cualquier sitio del mundo; con lo cual, cualquier rincón del mundo puede generar su propia energía y ser autosuficiente.

Los tipos de energía renovable que existen son:

Energía solar: La energía solar es aquella que obtenemos del sol. A través de placas solares se absorbe la radiación solar y se transforma en electricidad que puede ser almacenada o volcada a la red eléctrica

Energía eólica: En el caso de la energía eólica la generación de electricidad se lleva a cabo con la fuerza del viento.

Energía hidráulica: Utiliza la fuerza del agua en su curso para generar la energía eléctrica y se produce, normalmente, en presas.

Biomasa: Esta energía alternativa es una de las formas más económicas y ecológicas de generar energía eléctrica en una central térmica. La energía biomasa consiste en la combustión de residuos orgánicos de origen animal y vegetal

Biogás: El biogás es una energía alternativa producida biodegradando materia orgánica, mediante microorganismos

energía mareomotriz: (https://www.factorenergia.com/es/blog/eficiencia-energetica/energia-mareomotriz/) es la producción de energía (eléctrica) gracias a la fuerza del mar.

Energía geotérmica: la energía geotérmica es aquella que aprovecha las altas temperaturas de yacimientos bajo la superficie terrestre (normalmente volcánicos) para la generación de energía a través del calor

Programas necesarios para la realización

Programas que se podrían utilizar: Inventor, SolidWorks, Cade Simu

Se decide trabajar con Inventor para la parte del diseño y para la parte de la integración de energía renovable se plantea el uso de Cade_Simu

Inspeccionar ejemplos reales de bocetos y diseños de piladoras de arroz y maquinarias con energía renovable

Se investigó acerca de diseños de piladoras medianas y pequeñas ya existentes, con el fin de determinar parámetros en los cuales basarse para el diseño de la piladora para la comunidad de Paiyapales.

Se indagó la potencia eléctrica que requieren estos tipos de piladoras y la capacidad de producción en una medida de tiempo, además de reconocer qué elementos tienen internamente según el diseño.

Se analizó como energías renovables a los motores eléctricos cargados por paneles solares y a los motores Stirling.

En base a los datos investigados y a la demanda de arroz que poseen los habitantes de esta comunidad finalmente se puede determinar un diseño inicial para el siguiente avance y en futuras investigaciones se hablará sobre la implementación de la energía renovable en la piladora.

Piladoras de arroz

Piladora multigrano para pequeño y mediano productor:

Maquina ideal para Pilar diversos granos como maíz, arroz, café, frijoles, etc. Alto rendimiento.



1. Tolva de alimentación;
2. Rodillo de alimentación;
3. Rodillo de movimiento rápido;
4. Rodillo de movimiento lento;
5. Superficie de caucho;
6. Brazo regulador de los rodillos;
7. Manilla para regular la luz entre los rodillos;
8. Muelle de compresión;
9. Cubierta;
10. Polea motriz
11. Cubierta del equipo de accionamiento
12. Conducto de salida;
13. Base y armazón. Ampliación: separación de la cáscara entre rodillos.
Se utiliza para descascarar el arroz cáscara Se utiliza para descascarar el arroz cáscara y pulir, blanquear el arroz integral, y pulir, blanquear el arroz integral.

AJEX-One Pass Rice Mill:


La tolva de entrada tiene una malla de alambre vibrante que actúa como un simple limpiador de granos y prohíbe que entren objetos extraños grandes en la máquina

2. El sistema One Pass realiza el proceso completo de descascarillado, separación de la cáscara del arroz integral, blanqueamiento y eliminación del salvado, todo en una sola máquina
3. La superficie del grano se limpia con aire a alta presión y, por lo tanto, se obtiene un blanco brillante
4. La máquina es de construcción simple y de estilo
5. La máquina es fácil de instalar y de operar.
6. El ruido de funcionamiento es bajo.


MLGQ-C Descascaradora:


combined machine:


Piladora de arroz pequeña:



Piladora multigrano:


Piladora de arroz mediana con Rolo de Goma:


Piladora y moledora doble propósito:


Moledora de grano a disco:

Motores con energía renovable:

Motores con paneles solares

Hacer funcionar motores eléctricos de cualquier potencia con energía solar es viable, económico y mucho más habitual de lo que se cree.

la tecnología disponible en paneles solares e inversores, acompañada con la posibilidad de inyectar energía a una red existente, hacen posible que podamos utilizarla sin ningún tipo de problema y en múltiples configuraciones

En la industria donde hay acceso a red eléctrica, utilizar energía solar para suplementar el servicio reduce costos y suaviza el efecto de los picos de consumo que producen los motores

Las bombas de agua tradicionales que utilizan energía eléctrica de red o de grupos electrógenos, a menudo encuentran un gran aliado al utilizar paneles solares e inversores
específicamente | creados | para | bombeo.
Sobre todo en áreas de difícil acceso donde se requiere tener agua y se dificulta llegar con la red eléctrica, esta solución encuentra un lugar destacado

Se puede contar con motores de hasta 85Hp que se alimentan solo de paneles solares

Las posibilidades de la energía eléctrica producida por paneles fotovoltaicos es actualmente la misma que cualquier servicio eléctrico.



Motores Stirling

La principal ventaja de estos motores es que no es necesario quemar ningún combustible, como ocurre en las centrales termoeléctricas convencionales

El ciclo o tecnología Stirling se basa en un motor con el mismo nombre fundamentado en la termodinámica. Gracias a un foco frío y uno caliente, el gas en el interior de del motor se expande y se contrae realizando un trabajo y generando electricidad, es decir, tratándose de un motor térmico. En este caso, para producir energía limpia, el aporte de energía para el foco caliente proviene de una serie de grandes discos parabólicos que, orientados hacia un punto, reflejan la energía del sol. De este modo, la energía mecánica creada de la expansión y contracción en el interior del motor Stirling se convierte gracias a un alternador, en energía verde.



Desarrollo de lluvia de ideas de la solución del proyecto

Se ideó acerca de qué tipo de piladora de arroz se realizará según la cantidad de producción que realiza la comunidad de Paipayales. Si cuenta con 400 habitantes y el 40% de ellos se dedica al cultivo de arroz, quiere decir que 160 personas aproximadamente darán uso a las maquina piladoras de arroz. Esto puede dar ideas y estimaciones sobre las dimensiones y el alcance que podría tener la maquina a diseñar, considerando realizar máquina de una dimensión entre pequeña o mediana.

Estas máquinas por lo general trabajan con energía provenientes de combustibles fósiles, sin embargo se requiere trabajar con energía renovable, para lo cual se tiene el planteamiento de qué tipo de energía renovable se podría utilizar. Siendo una buena opción la energía solar por medio de paneles solares conectados a un motor eléctrico. Otras de las opciones podrían ser el uso de biomasa o biogás o energía geotérmica, sin embargo conocer el correcto funcionamiento de la obtención de estas energías no es tan fácil como el uso de paneles solares, los cuales podrían ser operados fácilmente por los agricultores de Paipayales.

La transmisión de movimiento del motor hacia la máquina se puede realizar mediante bandas y poleas, cadenas o correas sincrónicas. En este caso se decidió trabajar con bandas y poleas.

Se discutió acerca de los requerimientos de potencia de la máquina con el fin de establecer los parámetros del motor y del elemento de transmisión, en posteriores avances se determinarán estos parámetros en base a la producción que se realiza en la comunidad.

Se pretende realizar el diseño por medio de programas CAD como lo es Inventor para el dimensionamiento de cada pieza perteneciente a la. Con el fin de establecer las condiciones de falla de la máquina. En base a estos análisis se pretende seleccionar el material con el que se trabajará y en caso de desconformidades, realizar iteraciones tanto en el dimensionamiento como el material a usar.

En caso de ser necesario para el diseño de las piezas, se podría realizar un manufacturado de las mismas por medio de la extensión HSM de Inventor.

Finalmente se pretende hacer una cotización de todo los materiales y mano de obra necesario para la fabricación de la maquina

Referencias:

http://www.molino-de-arroz.com/Productos/linea-produccion-molino-arroz/1105.html

https://www.factorenergia.com/es/blog/noticias/energias-renovables-caracteristicas-tipos-nuevos-retos/ (https://www.factorenergia.com/es/blog/noticias/energias-renovables-caracteristicas-tipos-nuevos-retos/)

https://www.sangatiberga.com.br/es/produtos/arrozeras/descascaradora-de-arroz-sbr-sd

https://www.torotrac.com/product/OE-Piladora%20de%20Maiz-%20Piladora%20de%20Cafe%20-%20Piladora%20de%20Arroz (https://www.torotrac.com/product/OE-Piladora%20de%20Maiz-%20Piladora%20de%20Cafe%20-%20Piladora%20de%20Arroz)

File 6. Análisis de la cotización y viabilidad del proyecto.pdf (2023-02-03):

Aprovechamiento de recursos para un desarrollo sustentable en Paipayales

Análisis de precios y viabilidad de la máquina.

Integrantes: Marcelo Mendoza Hidalgo, Daniel Alvarado Peláez

Estimación de costos:

Tomando como referencia la base de datos realizada en previos avances sobre Potencia, costo y capacidad de piladoras en diferentes mercados, se hizo una filtración en la capacidad y potencia que este acorde a los parámetros solicitados, los cuales serían una capacidad de 100kg/h y potencia de 3HP respectivamente. Se realizo el siguiente grafico:


Gráfica1. Comparación Precio vs Capacidad vs Potencia
En la gráfica, las piladoras que superan el valor de $1000 ya incluyen el valor del motor, en nuestro caso estimamos, que al igual al caso 8 de la gráfica, que tiene un valor de $243 y una capacidad de 140 kg/h, contando con 3hp de potencia.

En este caso se consideró que un valor aceptable podría ser 240 sólo en la estructura de la máquina, pero se debe considerar que es la manufactura de un solo producto y no se genera la producción al por mayor y que se debe manufacturar cada pieza de manera individual, el costo aumentaría un 30%, por lo tanto, se considera que el precio de la estructura es aproximadamente 312 dólares.

Tabla: Estimación de costos

Elemento/Componente | Costo [$]
Estructura de la piladora (Sin motor)

$312


Motor Weg Monofásico De 3 Hp 2 Polos Motor Abierto 110/220


$246

Kit Bombeo Solar Trifásico 2,2KW 3HP

$447.805


Baterías x 15 | Unidad = $168.51 Total = $2527.65


Total de costo estimado: | $3533.45

Análisis final del proyecto:

En total se estimó que el precio de la máquina y su funcionamiento con energía solar tendrá un valor de aproximadamente 3500 dólares. Sin embargo, hay que considerar que la estructura de la piladora se estimó en base a la investigación de piladoras existentes de diferentes mercados y que posiblemente su valor sea establecido por las producciones en masa, por lo cual se tomó la medida de agregarle un valor adicional al ya seleccionado debido a nuestro mercado. Se recomienda que se debe hacer una cotización con compañías locales manufacturares para el realizado de las piezas, por ejemplo:

https://www.guimun.com/ecuador/negocios/5190/tecmefag-sa

https://www.barnadeck.com/maquinaria

No obstante, se realizó el dimensionamiento de ciertas partes de la máquina, rodamientos, poleas y bandas, con el fin de que ésta no se manufacturé desde cero y que se puedan seleccionar directamente de un proveedor como SKF. Adicionalmente se realizó el dibujo en 3D de la máquina en base a ejemplos de piladoras de baja potencia, en donde se puede obtener los planos para la fabricación de cada una de las piezas, pero recomendamos hacer un rediseño en un futuro, considerando parámetros adicionales de la maquina y su ambiente de trabajo.

En cuanto a la viabilidad de la maquinaria, considerando solo motor y estructura, que tienen un valor de $558 es factible su fabricación y aplicación en Paipayales haciendo uso de energía eléctrica, Pero tomando en cuenta que el fin del proyecto es el funcionamiento con energía renovable, en nuestro caso energía solar, se analizó su implementación con paneles solares, para lo cual se requiere el uso de baterías que almacenen dicha energía y permitan el uso de la piladora por alrededor de 8 horas al día, como fue requerido. Esto aumento el costo aproximadamente 6 veces en comparación a su aplicación con energía eléctrica, por lo cual no consideramos que sea factible poner en marcha la piladora con energía solar.

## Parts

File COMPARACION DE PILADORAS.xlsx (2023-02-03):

Aprovechamiento de recursos para un desarrollo sustentable en Paipayales
INTEGRANTES: |  | Marcelo Mendoza Hidalgo y Daniel Alvarado Peláez
Comparación: Potencia, costo y capacidad de piladores en diferentes mercados.
EMPRESA | Tipo | Precio ($) | Potencia (HP) | Capacidad (kg/h) | DESCRIPCION | CODIGO/MODELO/DISTINTIVO | TAMAÑO
Torotrac | DIESLE |  | 12 | 300 | MULTIGRANO | PS0000535 | MEDIANA
Torotrac | ELECTRICA 220V |  | 2 | 150 | MULTIGRANO | PS0000989 | PEQUEÑA
Torotrac | GASOLINA |  | 5.5 | 150 | MULTIGRANO | PS0000983 | PEQUEÑA
Torotrac | DIESEL |  | 20 | 800 | ARROZ GENERICA | PS0000144 | GRANDE
Torotrac | DIESEL |  | 20 | 800 | ARROZ SATAKE | PS0000143 | GRANDE
Torotrac | ELECTRICA 220V |  | 2 | 220 | ARROZ | PS0000145 | PEQUEÑA
Torotrac | GASOLINA |  | 5.5 | 160 | ARROZ | PS0000991 | PEQUEÑA
Mercado libre |  | 2867 | 24 | 2000 |  | JING GU: SB-30 | GRANDE
Mercado libre | ELECTRICA 220V | 640 |  | 150 | ARROZ |  | PEQUEÑA
Mercado libre | ELECTRICA 220V | 1800 | 15 | 1000 | ARROZ | JING GU: SB-10 | GRANDE
Mercado libre | ELECTRICA 400V | 22200 | 14.75 | 5000 | ARROZ | MLGQ36 | GRANDE
Clasf | ELECTRICA 220V | 1875 | 3 | 300 | PILADORA-TRILLADORA DE ARROZ | SPHNM-300 | PEQUEÑA
La Cobacha | ELECTRICA 110V | 650 | 2.68 | 120 | ARROS | POWER BULL: 6N40 | PEQUEÑA
Mercado libre | ELECTRICA 220V | 1195 |  | 300 | Trilladora Descascaradora Piladora De Arroz |  | PEQUEÑA
Mercado libre | ELECTRICA 220V | 1760 |  | 500 | ARROZ |  | MEDIANA
CROPER | ELECTRICA 220V |  | 7.5 | 120 | PILADORA-TRILLADORA DE ARROZ |  | PEQUEÑA
Mercado libre | ELECTRICA 220V | 1800 | 3 | 200 | ARROZ | 6N-J40 | MEDIANA
Mercado libre | ELECTRICA 220V | 1463 | 3 | 150 | MULTIGRANO | YUNINLI: J 4 | PEQUEÑA
Mercado libre | ELECTRICA 220V | 1514 | 3 | 200 | MULTIGRANO | YUNINLI: J 40 | PEQUEÑA
Mercado libre | ELECTRICA 220V | 1638 | 3 | 150 | MULTIGRANO | YUNINLI: J 220 | PEQUEÑA
Mercado libre | ELECTRICA 220V | 1743 | 4 | 200 | PILADORA-TRILLADORA DE ARROZ | YUNG: J 40 | PEQUEÑA
Alibaba | ELECTRICA 380V | 2500 | 7.4 | 3000 | PILADORA-TRILLADORA DE ARROZ | MLGT SERIES Rubber roll husker for rice milling plant | GRANDE
Alibaba | ELECTRICA 220V | 2000 | 7.4 | 2000 | PILADORA-TRILLADORA DE ARROZ | ANON mini rice huller | GRANDE
Alibaba | ELECTRICA 380V | 4572 | 14.75 | 5600 | MULTIGRANO | MLGQ51-001 | GRANDE
Indiamart |  | 243 | 20 | 1000 | ARROZ | Dharti | PEQUEÑA
Indiamart |  | 243 | 3 | 140 | ARROZ | Dharti | PEQUEÑA
Alibaba | ELECTRICA 220V | 120 | 3 | 180 | ARROZ | HELI 6N-40 | PEQUEÑA
Alibaba | ELECTRICA 380V | 1800 | 30 | 2000 | ARROZ | MG-N200 | PEQUEÑA
Alibaba | ELECTRICA 220V | 380 | 3 | 250 | ARROZ | HL-6N229 | PEQUEÑA
Alibaba | ELECTRICA 220V | 490 | 4 | 250 | ARROZ | KYM-RM6 3/4 | PEQUEÑA
Alibaba | ELECTRICA 380V | 600 | 7.4 | 1500 | ARROZ | FORMEND LM24.2C | PEQUEÑA
Alibaba | ELECTRICA 220V | 1000 | 2 | 150 | PILADORA-TRILLADORA DE ARROZ | DINGXIN 6HW47 | PEQUEÑA

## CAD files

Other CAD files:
CAD_Apiladora/Assembly1.iam
CAD_Apiladora/Assembly1/Design Accelerator/Correa trapezoidal1.ipt
CAD_Apiladora/Assembly1/Design Accelerator/OldVersions/Correa trapezoidal1.0001.ipt
CAD_Apiladora/Assembly1/Design Accelerator/OldVersions/Polea ranurada11.0001.ipt
CAD_Apiladora/Assembly1/Design Accelerator/OldVersions/Polea ranurada21.0001.ipt
CAD_Apiladora/Assembly1/Design Accelerator/OldVersions/Transmisión de correa trapezoidal1.0001.iam
CAD_Apiladora/Assembly1/Design Accelerator/Polea ranurada11.ipt
CAD_Apiladora/Assembly1/Design Accelerator/Polea ranurada21.ipt
CAD_Apiladora/Assembly1/Design Accelerator/Rodamiento1.iam
CAD_Apiladora/Assembly1/Design Accelerator/Transmisión de correa trapezoidal1.iam
CAD_Apiladora/Ensamblaje1.iam
CAD_Apiladora/OldVersions/Assembly1.0017.iam
CAD_Apiladora/OldVersions/Ensamblaje1.0006.iam
CAD_Apiladora/OldVersions/cernidera.0004.ipt
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

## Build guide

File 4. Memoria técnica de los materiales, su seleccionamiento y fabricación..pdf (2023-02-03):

Aprovechamiento de recursos para un desarrollo sustentable en Paipayales

Análisis de los elementos: materiales, seleccionamiento y fabricación.

Integrantes: Marcelo Mendoza Hidalgo, Daniel Alvarado Peláez

Partes de la máquina y su seleccionamiento o fabricación

Nombre | Selección | Diseño | Obtención | Observación
Mesa de trabajo | No aplica | Borrador Inventor | Se manda hacer: maquinado y soldado | Esta pieza fue dibujada en base a ejemplos reales. El material debe ser el adecuado para aguantar las vibraciones. Para su manufacturado se plantea soldar las piezas de metal.
Eje | No aplica | Borrador Inventor | Se manda a hacer: Maquinado y soldado | El eje fue dibujado en base a ejemplos reales. Será mandada a manufacturar la parte espiral con torneado y se soldará las protuberancias, con un tipo de metal no contaminante para alimentos.
Rodamientos | Selecciona do | Dimension ado (SKF) | Compra | Esta pieza fue diseñada y seleccionada en base a los parámetros de transmisión y a la calculadora de SKF
Bandas y poleas | Selecciona do | Diseñada (SKF) | Compra | Esta pieza fue diseñada y seleccionada en base a los parámetros de transmisión y al manual de SKF
Armadura | No aplica | Borrador Inventor | Se manda hacer: maquinado y soldado | Esta pieza fue dibujada en base a ejemplos reales. El material puede ser un material básico
Cernidora | No aplica | Diseñada | Se manda hacer: manufacturado | Esta pieza fue dibujada en base a ejemplos reales. Se hará con un material no contaminante para el alimento
Motor | Selecciona do | No aplica | Compra | Es un motor seleccionado acorde a los parámetros de potencia y velocidad requeridos.

Kit de uso de energía solar | Selecciona do | No aplica | Compra | Es un kit de ejemplos para el uso de energía solar, en la alimentación de la piladora.
Baterías | Selecciona do | No aplica | Compra | Para almacenar energía y alimentar el motor por unas 8 horas.

Determinar el material usado cada una de las piezas

Material | Pieza | Comentario
Hierro fundido | Mesa de trabajo | Es un material de bajo costo, Es conocido por sus excelentes propiedades de amortiguación de vibraciones. Se usará en las piezas que no se encuentren en contacto directo con el alimento, puesto que en un ambiente húmedo y con presencia de polvo, pueden tener oxidación y ocasionar daños en el alimento. Es un metal muy flexible, tenaz, maleable y dúctil de gran soldabilidad y tiene buena maquinabilidad

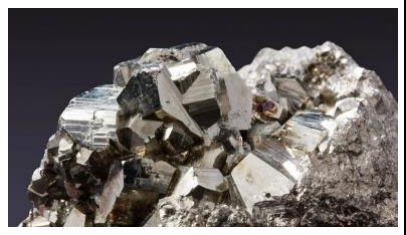
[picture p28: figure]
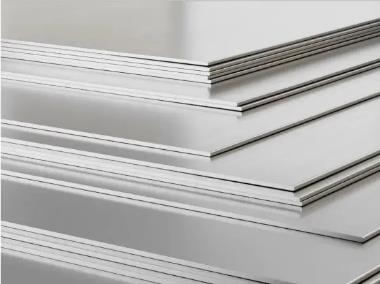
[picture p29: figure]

Acero inoxidable 316

Armadura

El acero inoxidable 316 es un acero inoxidable austenítico de cromo-níquel que contiene entre dos y 3% de molibdeno. El contenido de molibdeno aumenta la resistencia a la corrosión, mejora la resistencia a las picaduras en soluciones de iones de cloruro y aumenta la resistencia a altas temperaturas. Adicionalmente, es particularmente efectivo en ambientes ácidos y sirve para proteger contra la corrosión causada por los ácidos sulfúrico, clorhídrico, acético, fórmico y tartárico, así como los sulfatos ácidos y los cloruros alcalinos.
Los aceros inoxidables son resistentes a la corrosión en muchos medios y de ese modo

Eje

Cernidora | pueden estar con los alimentos sin sufrir degradación en su composición química.
Baterías ácido-plomo | Batería

Tiene el objetivo de acumular la energía eléctrica (https://solar-energia.net/electricidad) generada por las placas solares fotovoltaicas. Proveen una intensidad de corriente (https://solar-energia.net/electricidad/corriente-electrica/intensidad-de-corriente) superior que la que puede ofrecer un panel fotovoltaico (https://solar-energia.net/energia-solar-fotovoltaica/elementos/panel-fotovoltaico) en funcionamiento. Las baterías de ácido-plomo son ideales para paneles solares por la relación de precio por energía disponible. Su eficiencia está entre un 85-95%. La vida útil de una batería para instalaciones solares suele ser de unos 10 años al ser usadas correctamente.

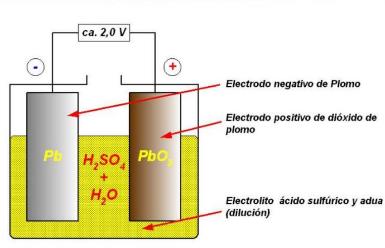
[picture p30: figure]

SKF se reserva los
derechos de fabricación

Rodamiento
s

Bandas y
poleas

SKF se reserva el derecho a efectuar mejoras continuadas sobre los productos SKF con respecto a materiales, diseño y métodos de manufactura, así como cambios necesarios por desarrollos tecnológicos.

Referencias:

https://metalium.mx/hierro-fundido

https://respuestas.me/q/por-que-los-metales-no-amortiguan-las-vibraciones-33610767745
